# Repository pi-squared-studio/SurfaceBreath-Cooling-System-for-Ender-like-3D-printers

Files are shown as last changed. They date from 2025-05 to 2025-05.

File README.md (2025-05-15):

# SurfaceBreath Cooling System (for Ender-like 3D-printers)
_Simple thing to increase quality of yours 3D prints_

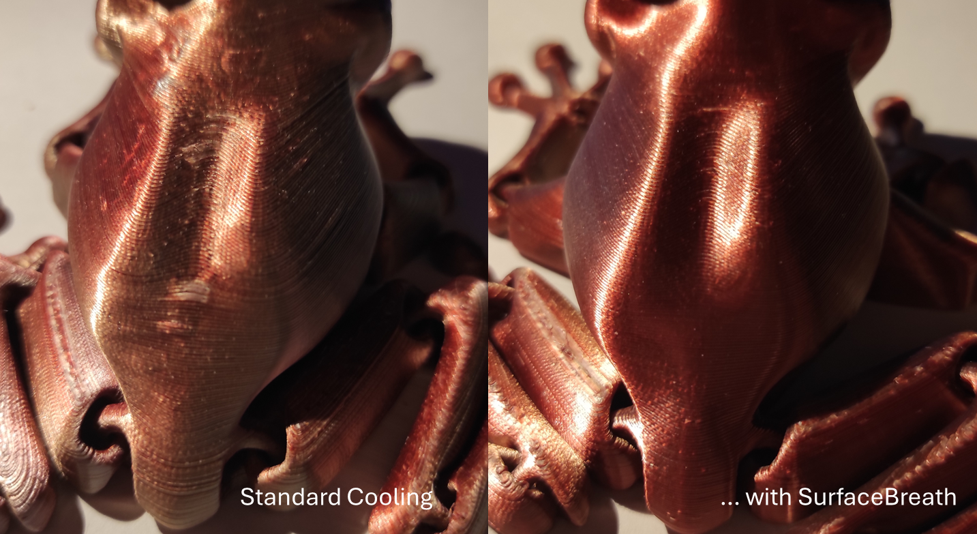
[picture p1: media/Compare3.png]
Compare the cooling 3


## Features

**Description:**	This device is an additional cooler for the printed part to improve product quality. The main purpose is to ensure uniform cooling of the upper layer of the part, against the formation of overhangs bending upwards.

**Designer:**  π²Studio

**Designed for:**	Voxelab Aquila C2

**Compabtility:**	Creality Ender-3 and its clones with 235 mm bed width

**Mount:**		at backside of X-axis rail. The height of the duct above the bed is 5 mm when using a standard nozzle downgrade.

## Overview

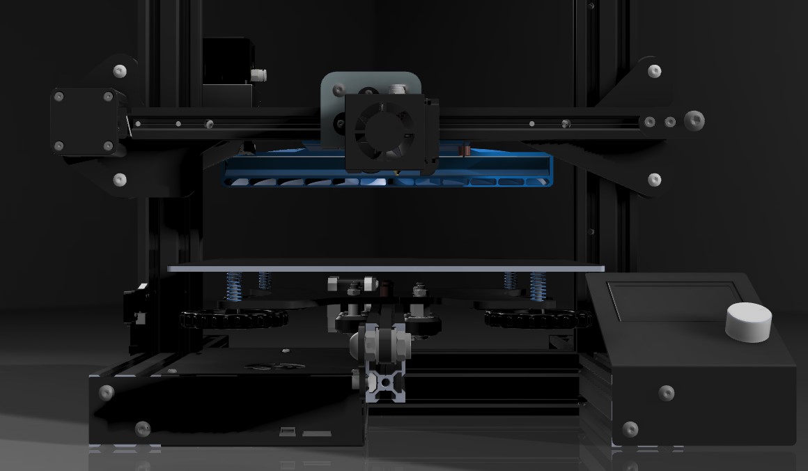
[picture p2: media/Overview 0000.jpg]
Overview Front


In my practice, I have encountered the problem of breaking off a part of a printing model (or even the entire model) from the bed during the printing process. When I began to study this problem, it turned out that the curved overhangs rising up from the temperature were to blame for everything. This was due to the fact that the part was still heated from the table (although its temperature was lower than the temperature of the softened plastic), and the additional heat radiated from the hotend, which was enough for this process to take place. Even the cooling of the standard fan, baked at 100%, was not enough to stop this process, which could start a few centimeters away from the cooling stream.
The second problem, after I adjusted all the temperature and speedy settings, and the parts no longer came off the bed, was that slightly protruding overhangs could spoil the appearance of the surfaces. This became especially noticeable when using silk PLA in art projects. Defects occurred on both external and internal overhangs. It could either be a non-glossy, furrowed surface, or random "warts" appeared on it.
It was decided to develop an additional cooling system to the existing one in order to remove such defects. This is not a replacement for the standard one, but only serves to optimize the temperature regime at the printing surface. In other words, it "freezes" the topmost layer from accidental additional heating. SurfaceBreath has no additional effect on the main fan flow.

_SurfaceBreath_ creates a very weak laminar flow along the entire print surface, similar to light breathing, and displaces stagnant thermal zones that are not affected by the cooling of the main fan.
Now your printer will not face the problem of the extruder nozzle colliding with the printed part, and its possible separation from the bed!

_SurfaceBreath_ was tested by me for PLA plastics and showed amazing results. According to my estimates, the adhesion of the part itself to the bed has even improved.
There are no definite results with other plastics yet, as I have always had a great experience with PETG.
ABS-like plastics, yes, the small parts like they've started to look a little smoother. I have not tried with large parts made of this plastic, since I do not have a normal thermal case.

In addition, I made another version of the duct with a light. It is convenient to use it to control the printing of the first layer, as it creates contrasting lighting. It can also be used as torch during maintenance.
It uses standard LED strips up to 12 mm wide.

Special set spacers with thicknesses of 3, 5, 10, 20 and 50mm are used for mounting to the X-axis frame.
A set of the spacers of various thicknesses allows you to fix the duct at almost any acceptable distance from the frame so that they don't touch various other printer mechanisms. In the version with the duct without a lamp, it will be enough for a standard printer with direct extruder to make just one spacer with 3mm thickness. To raise the duct to a height of 5 or 10 mm, use an appropriate spacer with a thickness of 15 mm.

_SurfaceBreath_ can also be used as a fan to quickly cooldown the bed, a fan that will blow over the extruder elements from accidental melting during idle time, or to provide of air microcirculation in the thermoenclouse, if such is used.

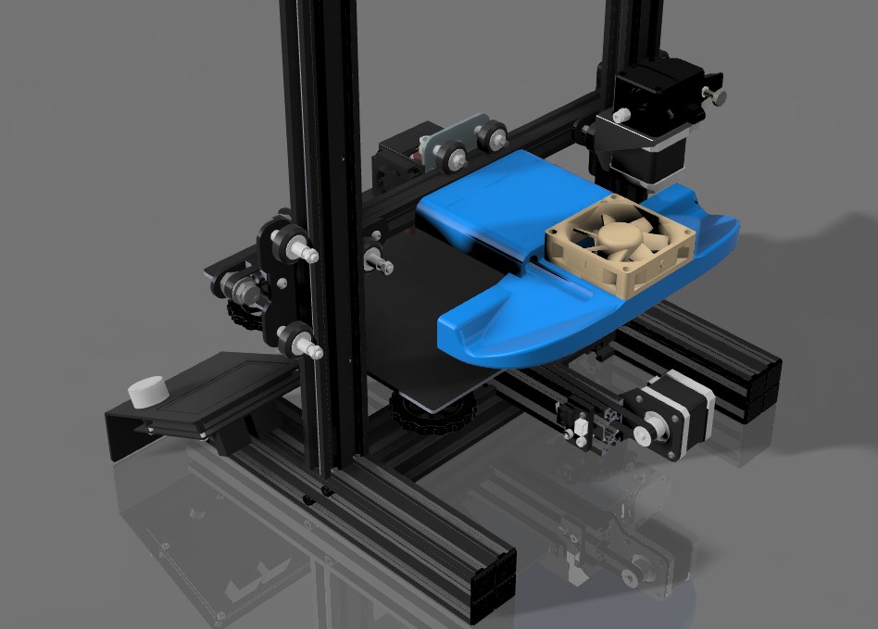
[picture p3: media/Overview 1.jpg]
Overview Front


## Bill of materials

### Base parts
1. 70X0 axial fan - 1 pc. I used the 7020 quiet model from an old 12-volt computer cooler, but you can use any other suitable 70x70mm size (for example, 7010, 7015 or 7030...) with any power supply voltage. If it is 24V, then it will be possible to power it from a printer's PSU. If you get one with a different voltage, then make a voltage stabilizer for it or take a separate power supply. It's a good idea to use any speed control for this fan.
2. M5 EU#20 profile T-nuts - 2 pcs. For attach the duct to frame.
3. Self-tapping screw OD 3mm - 4 pcs. For screwing of the fan to duct. Their total length should be 5-10mm + the thick of the fan.
4. Self-tapping countersunk screw OD 3mm  - 2 pcs (Optional. For mostly screwing thin, near the duct, 3 or 5mm spacer). Their total length should be 8-12mm + the distance of attached spacer.
5. Any suitable desired LED strip with a width of not more than 12mm, and a length of not more than 230mm, and a thickness of not more than 2.5mm. (For the option with a light). A dimmer is also welcome.

### Parts for usual variant without rising spacer
6. M5 bolts - 2 pcs. Their total length should be 6-8mm out of contact surface + the distance of all used spacers. You may use a set of M5x10x1 washers for compensate extra length of their bolts. In other words, the ledge of the bolt deeper into the frame should not exceed 5mm.

### Parts for variant with rising spacer
6. M5 bolts - 2 pcs. Their total length should be 13-15mm out of contact surface + the distance of all used spacers before rising one.
7. M5 hex nut - 2pcs.
8. M5x10 bolts - 2 pcs. For attaching a rising part to the frame.

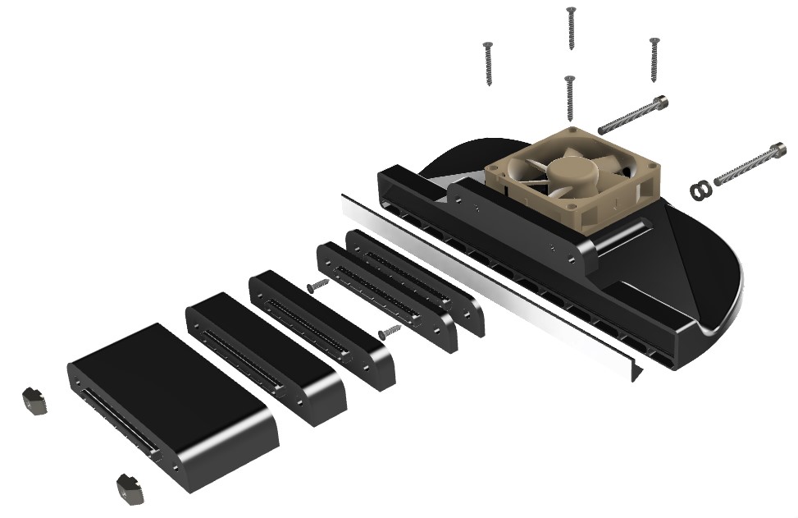
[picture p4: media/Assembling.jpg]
Assembling Rule


## Print conditions

The duct and spacers are printed from the plastic from which subsequent products will be printed, and this material must withstand the temperature of a heated bed. ABS will be an ideal option for everyday tasks, but you will need to ensure the internal strength of the part so that it does not come off the bed and does not get upset during printing.
0.2 - layer thickness (0.3 if you want quickly print), 3-4 wall loops, 10% infill enough for duct - the part does not experience heavy loads. For spacers need to increase infil upto 50%.
Print without support, but make sure that the overhang bridges print well.  A raft is allowed to increase the strength of the attachment to the bed.

The diffusing glass is printed from transparent PETG. 2 walls. Different density fillings can be applied for various dispersion. I prefer 20% gyroid filling.

## Disclaimers

This model was developed independently by autor and was based on well-known physical principles and phenomena.
Everything described in this article is not a universal case for all such reasons, but is considered only from the perspective that specific experience has been gained.
Any consequences with the use of this device are attributed to the follower who repeated this idea.
The model is in slow development and modification and it may contain some flaws. 
Check all dimensions and mounting options before you print these parts!
Please note that repeated it is possible that the model may be changed or reinterpreted, embodied in a new form.
All new modifications or additional improvements will be posted on this page: https://github.com/pi-squared-studio/SurfaceBreath_Cooling_System

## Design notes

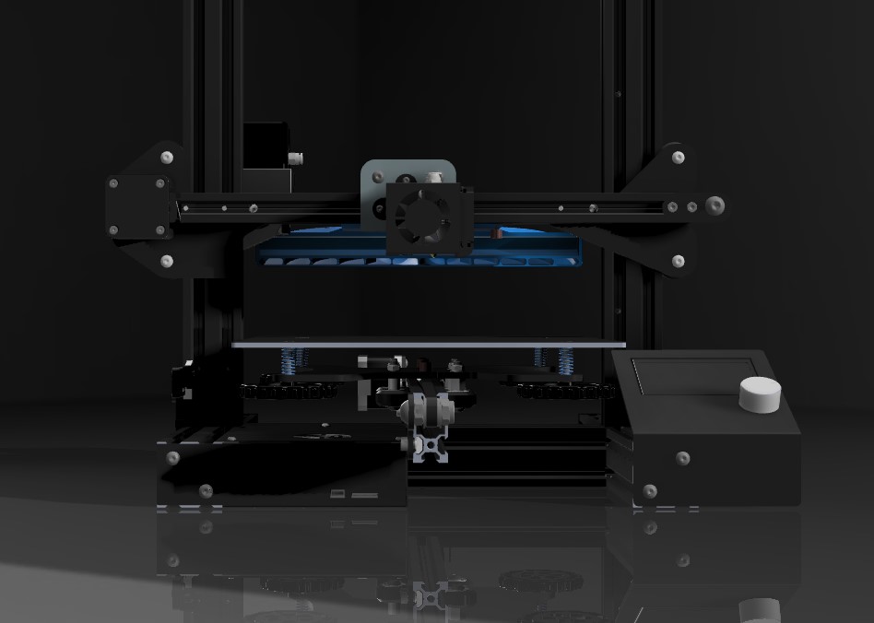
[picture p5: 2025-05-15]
media/Overview 0.jpg

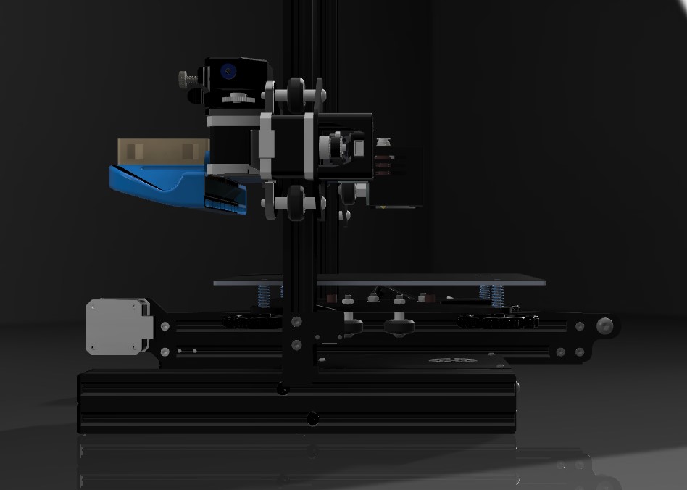
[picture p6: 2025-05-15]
media/Overview 3.jpg

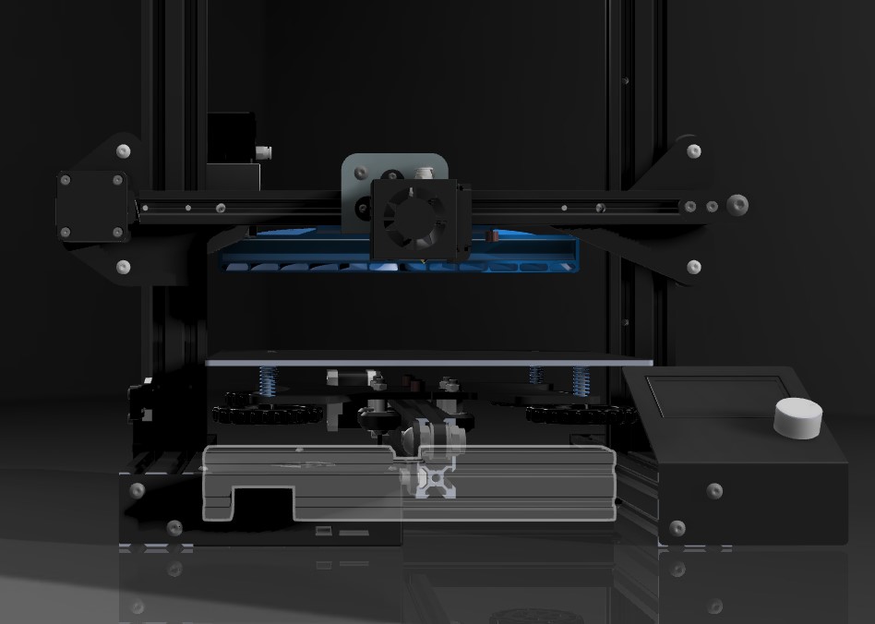
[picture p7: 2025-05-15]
media/Overview 000.jpg

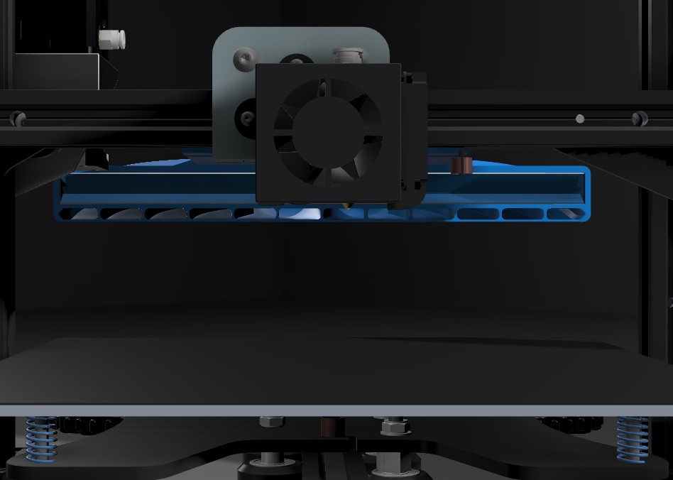
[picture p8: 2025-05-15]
media/Overview 00.jpg

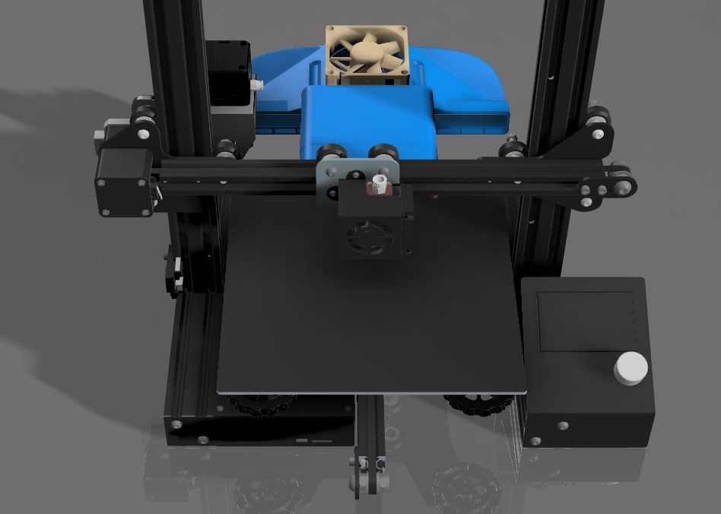
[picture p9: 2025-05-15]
media/Overview 2.jpg

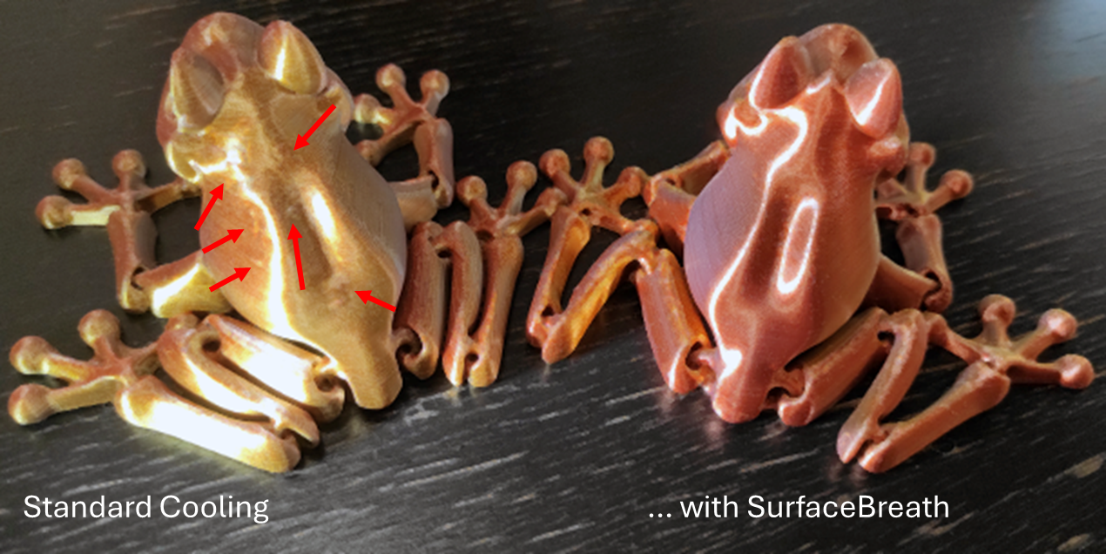
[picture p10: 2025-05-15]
media/Compare1.png

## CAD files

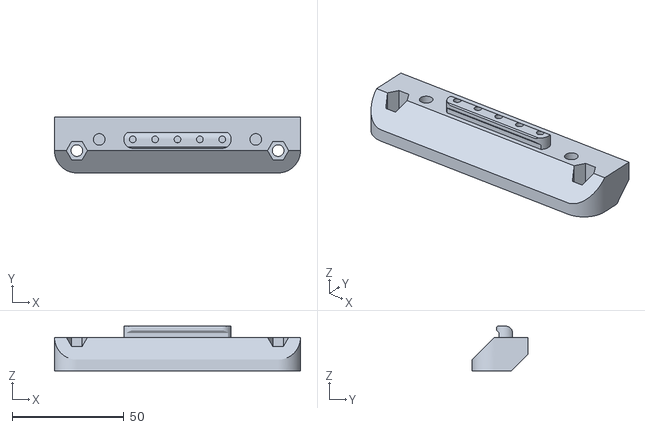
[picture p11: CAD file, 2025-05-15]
v1/SurfaceBreath Spacer 15 with rise +5 v1.2.stl
110.0 x 25.0 x 20.0

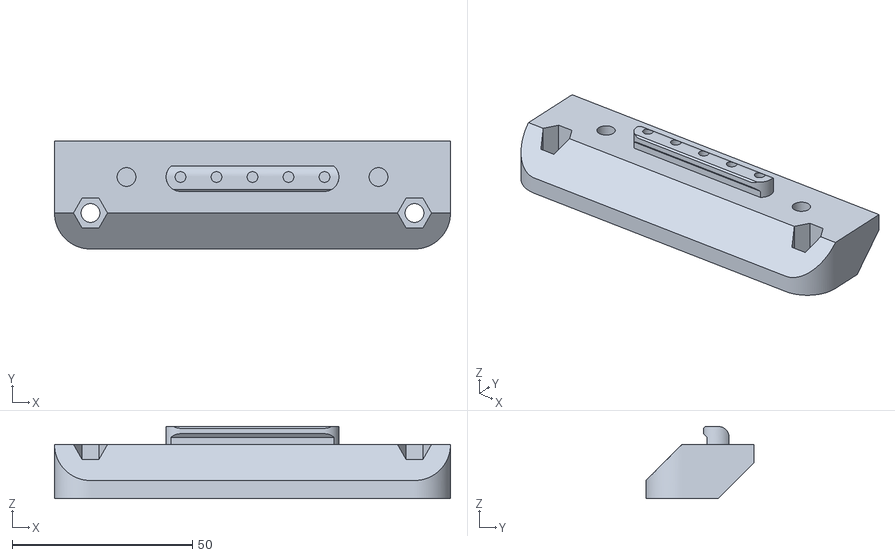
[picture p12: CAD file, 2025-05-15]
v1/SurfaceBreath Spacer 15 with rise +10 v1.2.stl
110.0 x 30.0 x 20.0

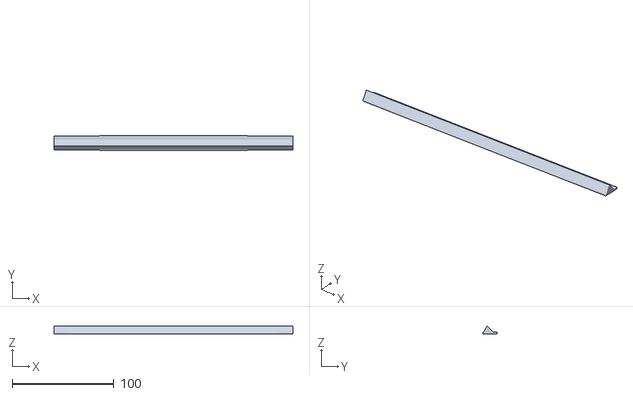
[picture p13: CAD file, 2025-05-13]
v1/SurfaceBreath Diffuser Lens 240 v1.0.stl
234.8 x 14.3 x 8.27

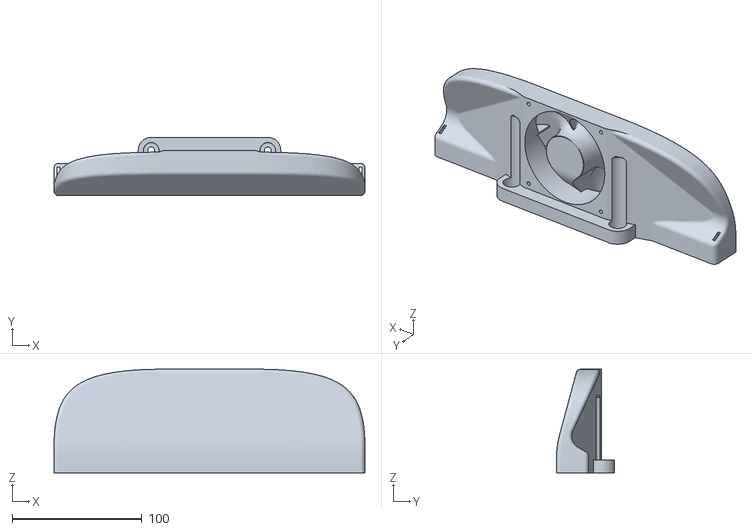
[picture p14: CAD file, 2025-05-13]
v1/SurfaceBreath Duct 240-70 with Light v1.5.stl
240.0 x 45.0 x 80.0

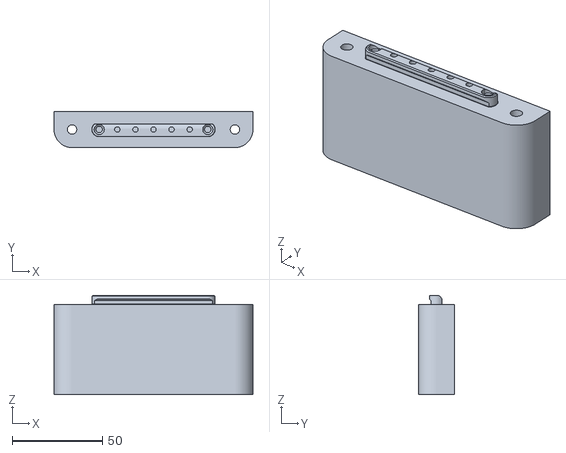
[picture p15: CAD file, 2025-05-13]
v1/SurfaceBreath Spacer 50 v1.2.stl
110.0 x 20.0 x 55.0

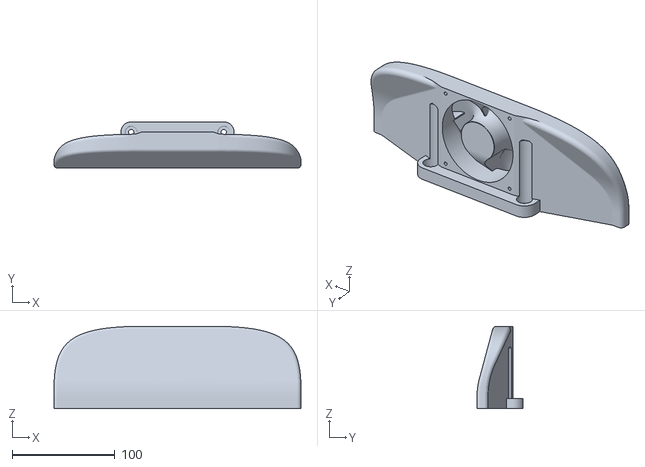
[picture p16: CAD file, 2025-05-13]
v1/SurfaceBreath Duct 240-70 v1.5.stl
240.0 x 45.0 x 80.0

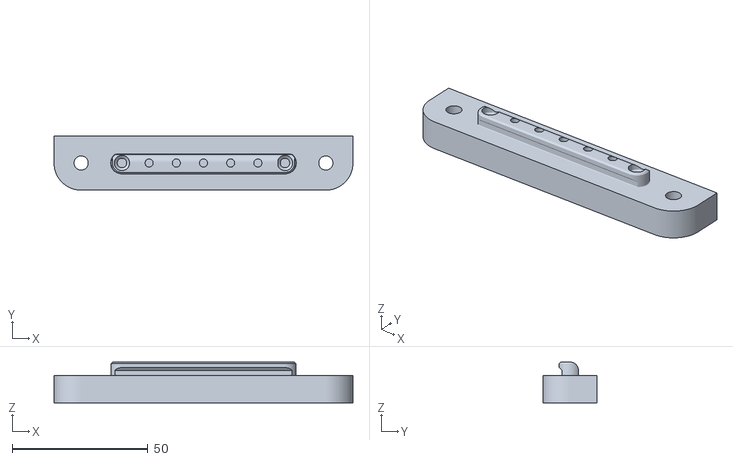
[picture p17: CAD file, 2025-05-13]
v1/SurfaceBreath Spacer 10 v1.2.stl
110.0 x 20.0 x 15.0

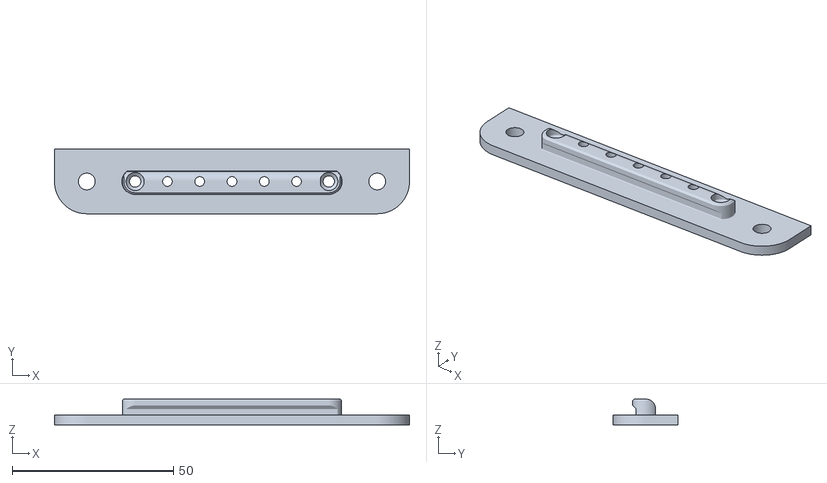
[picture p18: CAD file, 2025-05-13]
v1/SurfaceBreath Spacer 3 v1.2.stl
110.0 x 20.0 x 8.00

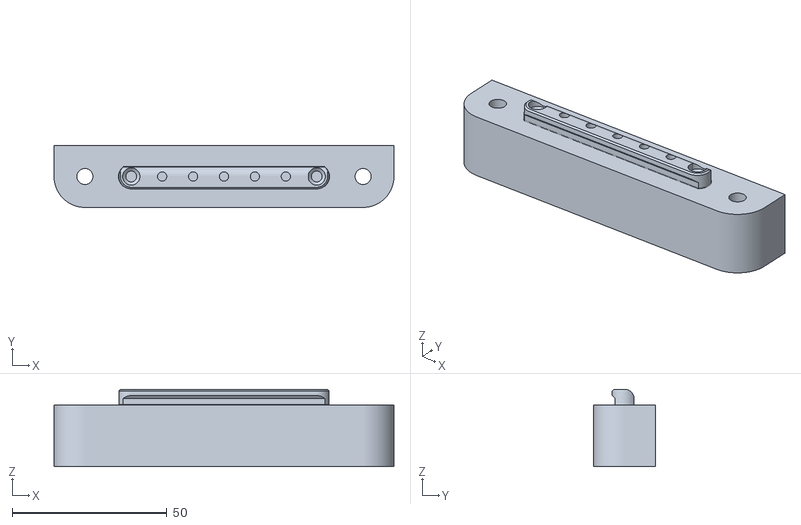
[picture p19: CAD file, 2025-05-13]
v1/SurfaceBreath Spacer 20 v1.2.stl
110.0 x 20.0 x 25.0

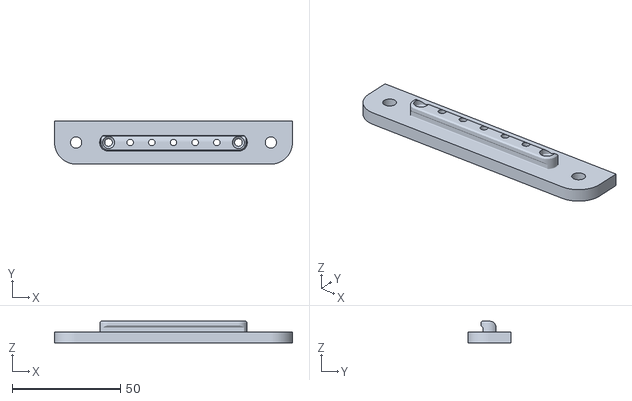
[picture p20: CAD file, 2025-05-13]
v1/SurfaceBreath Spacer 5 v1.2.stl
110.0 x 20.0 x 10.0
